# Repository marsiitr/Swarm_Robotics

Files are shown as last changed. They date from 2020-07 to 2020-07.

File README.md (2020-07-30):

# Swarm_Robotics
## Srishti 2020
<p align="center">
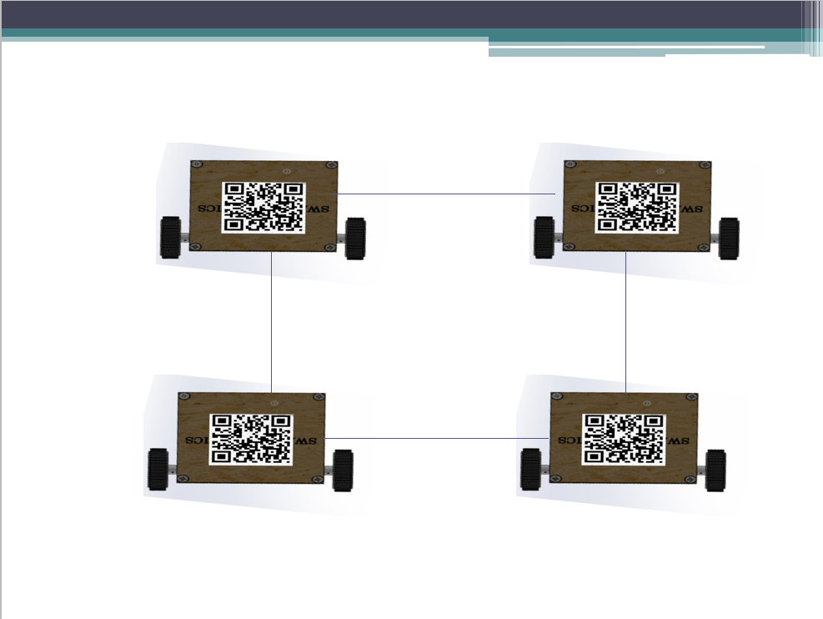
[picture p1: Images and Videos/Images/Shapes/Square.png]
  
</p>

## Abstract
<p align ="justify">Swarm robotics is an approach to the coordination of the multiple robots as a system which consist of large numbers of mostly simple physical robots.  Only through their interactions a collective behavior emerges that is able to solve complex tasks. These characteristics lead to the main advantages of swarms: adaptability, robustness, and scalability. Under this excuse we made multiple bots which coordinate among themselves to form different shapes.</p>

## Motivation
<p align ="justify">As swarm of ants work in unison to achieve an intimidating task, similarly multiple bots can work in unison to achieve a seemingly difficult task. As the newbies, out of curiosity we choose to work on the same.</p>

## Working
<p align ="justify">Open cv facilitates the process of reading QR codes, including loading images from disk, grabbing a new frame from a video stream, and processing it. Important libraries we imported are pyzbar, argparse and cv2.
    The ZBar library will decode the barcode or QR code. OpenCV can come back in to perform any further processing and display the result. For Python, we use pyzbar, which has a simple decode function to locate and decode all symbols in the image. The decode function simply wraps pyzbar’s decode function and loops over the located barcodes and QR codes and prints the data. The decoded symbols from the previous step are passed on to the display function . If the points form a quad ( e.g. in a QR code ), we simply draw the quad. If the location is not a quad, we draw the outer boundary of all the points ( also called the convex hull ) of all the points. This is done using an OpenCV function called cv2.convexHull. Finally, the main function simply reads an image, decodes it and displays the results.</p>
<p align="center">
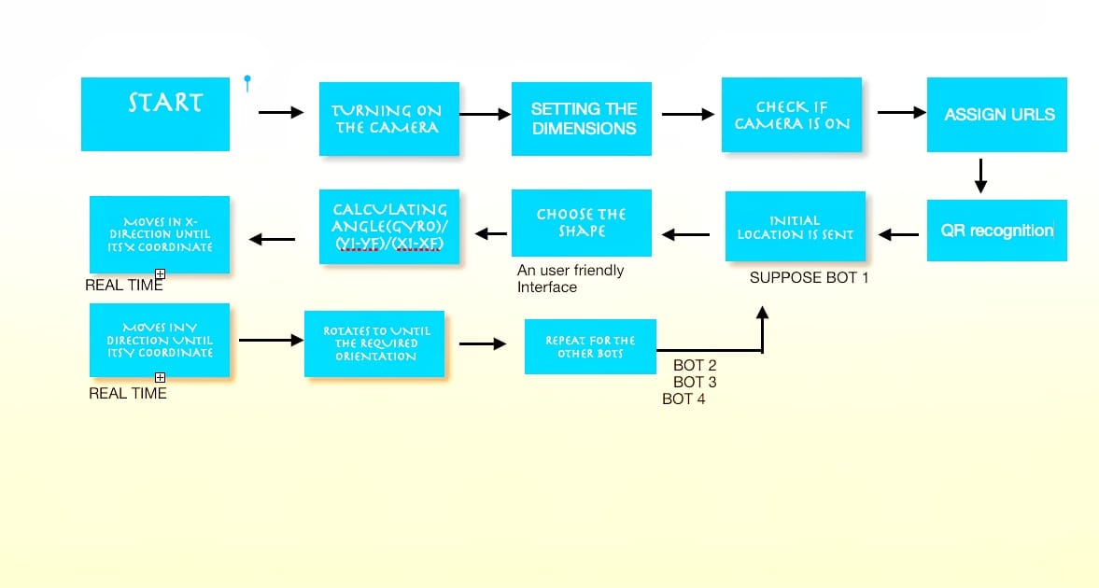
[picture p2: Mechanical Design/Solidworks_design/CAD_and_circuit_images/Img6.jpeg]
  
</p>
<p align ="justify">Firstly ,a function handleSpecificArg() is defined that receives data that is sent by the python code that is doing image recognition. Python returns the data in the form of string which is then sent to the NodeMCU. All of the NodeMCUs are connected to the hotspot of the same laptop so it directly sends the data to each NodeMCU.
  Then several functions such that backward(), forward(), etc are defined that helps the bots to move. Then a function get_gyro() is defined that gives the angle turned by bot. Then setup of different pins takes place. Then the function data() gets all the coordinates and the current angle from x-axis and which shape is to be made.
Then the real loop function starts. First we get data from the camera . Then the bot starts to rotate until it is turned in the direction of target position . Then it starts to move forward until it reaches the target position on reaching the target position it starts rotating until it reaches the required orientation. All the bots do the same to make the required shape.</p>

## Mechanical Aspect of the Design
<p align ="justify">This project consists of four mechanically identical bots which move in unison to form the shape specified by the user. But each of the bot has a unique identity because of the unique QR code pasted on its roof.</p>
<p align="center">
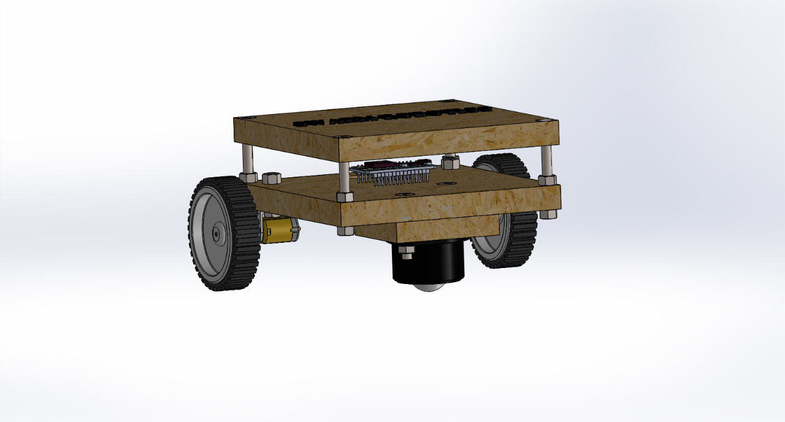
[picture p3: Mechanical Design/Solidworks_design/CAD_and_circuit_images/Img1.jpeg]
  
</p>

<p align ="justify">Each bot has 2 sheets of ply one over the other with electrical components between them. A single bot consists of 2 normal wheels at the back, 1 castor wheel at the front and 2 L-brackets for holding motors in them.</p>

<p align="center">
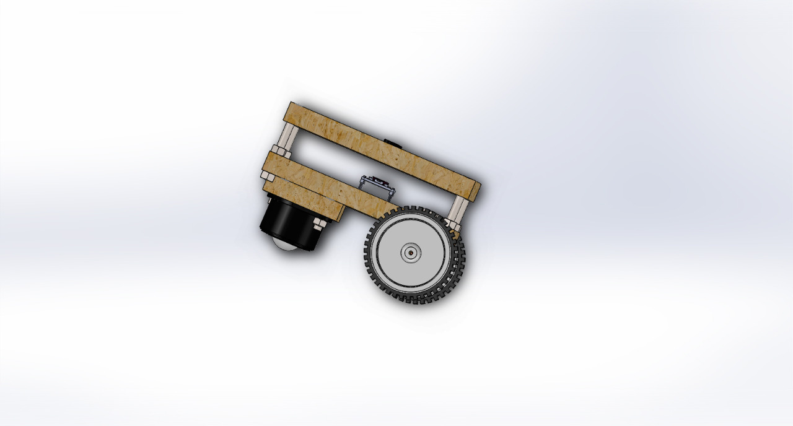
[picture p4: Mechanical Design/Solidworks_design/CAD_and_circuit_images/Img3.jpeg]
  
</p>

## Electronics Aspect of the Design
<p align ="justify">In each of the bot, the microcontroller used is ESP8266(NodeMCU). For angle detection fron the initial position for a particular bot, a gyroscope sensor(particularly MPU-92/65 is used. For controlling the motors, a motor driver(particularly L298) is used in each bot.</p>
<p align="center">
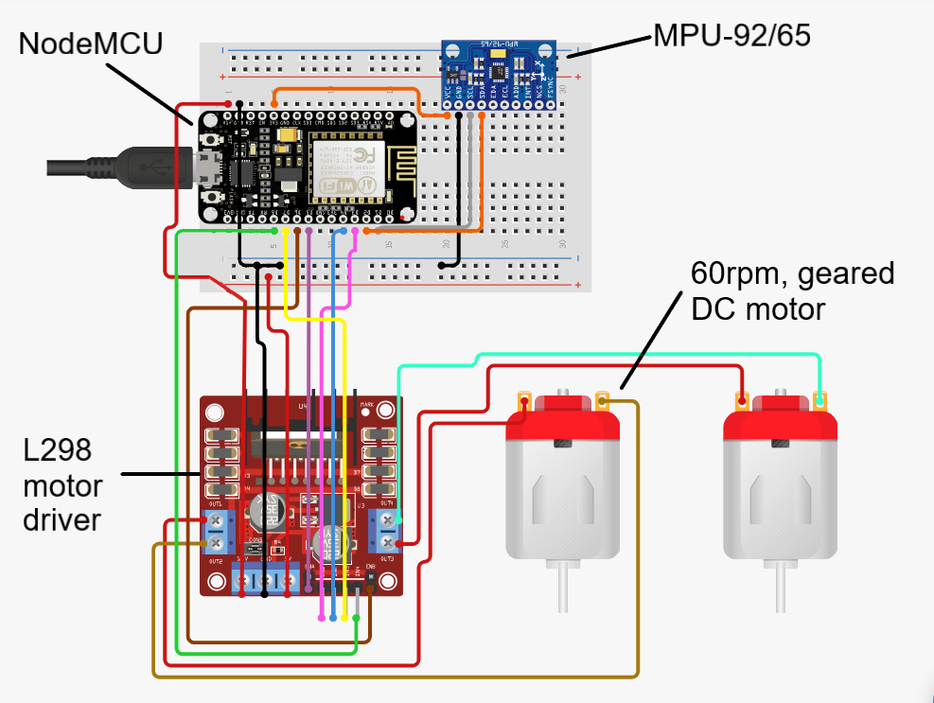
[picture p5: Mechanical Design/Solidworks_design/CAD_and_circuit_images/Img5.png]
  
</p>
  <p align ="justify">Initially each bot is set to a particular same direction, but when the user calls for a shape using a user friendy interface, each bot is assigned its final coordinates in the field of view of the overhead camera. Thus each bot reaches to its final position one by one. And the final shape is achieved.</p>

## Cost Structure

| Part | Quantity | Cost per unit | Total cost |
|---|:---:|:---:|---:|
| ESP8266 (NodeMCU) | 4 | 330 | 1320 |
| L298  (Motor Driver) | 4 | 250 | 1000 |
| 60rpm DC Motor | 8 | 200 | 1600 |
| MPU 92/65 (Gyroscope) | 4 | 300 | 1200 |
| Overhead Camera (WebCam) | 1 | 3000 | 3000 |
| 12V Li-polymer Battery | 4 | 2000 | 8000 |
| Jumpers | 60 | 5 | 300 |
| Nut & Bolt (Medium) | 16 | 5 | 80 |
| Nut & Bolt (Long) | 16 | 10 | 160 |
| L - Brackets | 8 | 15 | 120 |
| Normal Wheels | 8 | 30 | 240 |
| Castor Wheels | 4 | 25 | 100 |
| PlyWood | 1 | 280 | 280 |
| Miscellaneous | - | - | 600 |
| Total | | | Rs.18000/- |

## Applications
Potential applications of swarms are many. To list the few:
* Tasks that demand miniaturization, like distributed sensing tasks in micromachinery or the human body.
* One of the promising use of the swarms is in disaster rescue missions.
* Swarms can be used in traffic handling.
* Swarms can form different shapes and designs so they can reach forbidden area.

## Limitations
* Formation of limited number of shapes.
* Initial relative distance  of the bots depends on the field of view of the camera use.
* Dependency on QR code recognition.
* Gyroscope must be used with intense care, as a slight slip of gyro in any of the direction, may give a large error in angle calculation.

## Future Improvement
* Many more shapes can be added to the list.
* Providing the sensors to prevent collision.
* Use of PID, to improve the movement of the bots.
* Assembling(to form the shape), independent of their initial positions.
* Use of GPS instead, to reach their destination.

## Team Members

1. [Paritosh Sanadhya](https://github.com/Pasa1912)
2. [Prathamesh Bhaktan](https://github.com/prathamb)
3. [Samiksha Jain](https://github.com/samiksha-jain003)
4. [Sarthak Malik](https://github.com/ganzagun)
5. [Vidhi Mittal](https://github.com/Vidhi-mittal01)

## Mentors
1. [Annu Shree](https://github.com/annushree21)
2. [Shubhanshu Agarwal](https://github.com/Shubhanshu07)

## References
* [OpenCV Python Tutorial For Beginners](https://www.youtube.com/playlist?list=PLS1QulWo1RIa7D1O6skqDQ-JZ1GGHKK-K)
* [Stack Overflow](https://stackoverflow.com/)
* [Pyimagesearch](https://pyimagesearch.com/)
* [Arduino](https://www.arduino.cc/)

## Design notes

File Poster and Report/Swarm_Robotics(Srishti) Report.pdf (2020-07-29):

# REPORT

# Event: Srishti 2020 Indian Institute Of Technology Roorkee

# Project name: Swarm Robotics

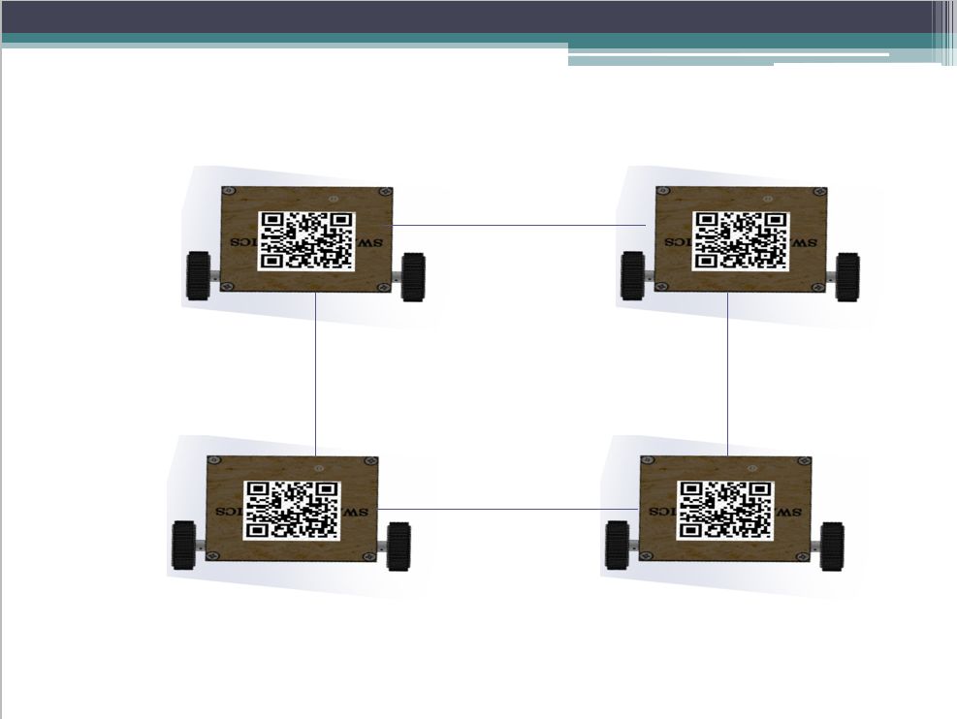
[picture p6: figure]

# Team Members and Mentors :

Team Members | Enroll. no.
Paritosh Sandhaya | 19115083
Prathmesh Bhaktan | 19117088
Samiksha Jain | 19312028
Sarthak Malik | 19118073
Vidhi Mittal | 19113156

# Mentors

## Shubhanshu Agarwal Annu Shree

# OVERVIEW

Every year Models And Robotics Section (MARS) IIT ROORKEE organises annual technical fest “SRISHTI”, especially for freshers, where they can sharpen their technical and entrepreneurial skills.
Group of few diligent members are assigned to certain projects within a few months, under the mentorship of intuitive MARS members. We got the window of opportunity to be the part of this technical fest where we came out of the idea of building swarm robots , which coordinate among themselves to form various shapes which includes square, triangle, some alphabets and numbers etc.

# MOTIVATION

As a swarm of ants work in unison to achieve an intimidating task, similarly a swarm of robots can work in unison to achieve seemingly impossible tasks. As the enthusiastic newbies we were fascinated by this idea and decided to work on the same.

# ABSTRACT

Swarm robotics is an approach to the coordination of the multiple robots as a system which consists of large numbers of mostly simple physical robots. Only through their interactions a collective behavior emerges that is able to solve complex tasks. These characteristics lead to the main advantages of swarms: adaptability, robustness, and scalability. Under this excuse we made multiple bots which coordinate among themselves to form different shapes.

# WORKING

↓

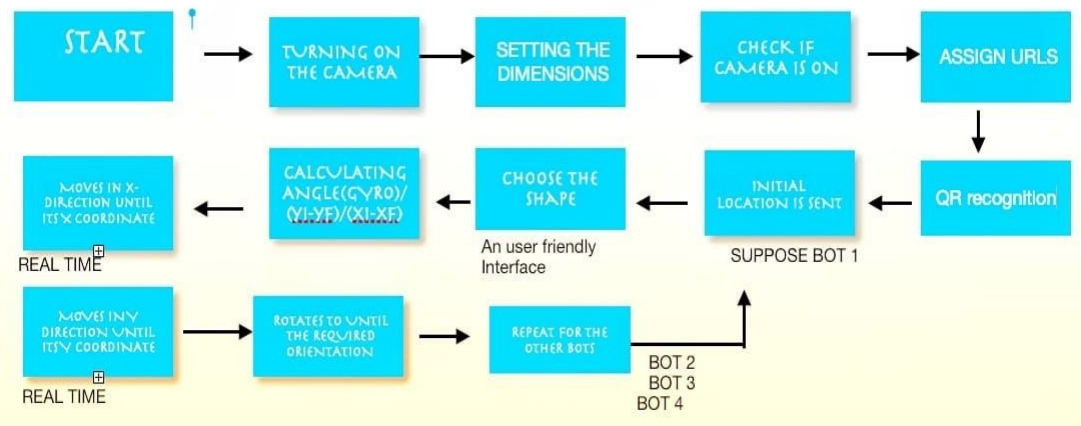
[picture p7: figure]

# Mechanical Aspect of the design:

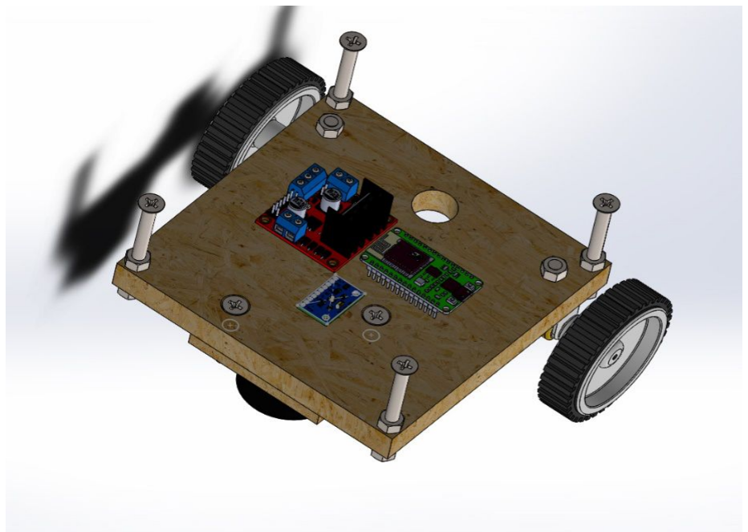
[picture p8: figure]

Angled view of the bot

## Details of Components Used:

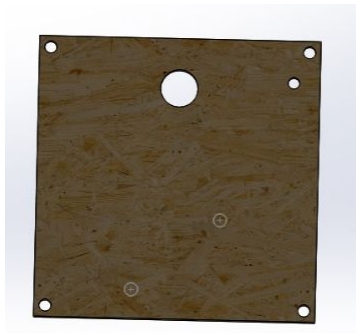
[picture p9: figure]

## 1. Plywood

Larger Plywood acts as a base for assembling all parts of swarm robots and provides support to all items. It has a size of 150x150x15 mm, and has a hole of 20mm on it for connecting motors with Arduino.

Larger Plywood is also used to make roof of robot which has QR Codes for scanning purpose

Smaller plywood is used to level the castor wheel with normal wheels and provide stability to bot.

Its size depends on the size of castor wheel , in our case, from the standard cad model of caster wheel, the thickness of smaller plywood is 13.8mm.

## 2.L-brackets

L-brackets are used for mounting motors and holding it in the correct fixed position. It is mounted on a plywood base with the help of 3mm nuts and bolts.

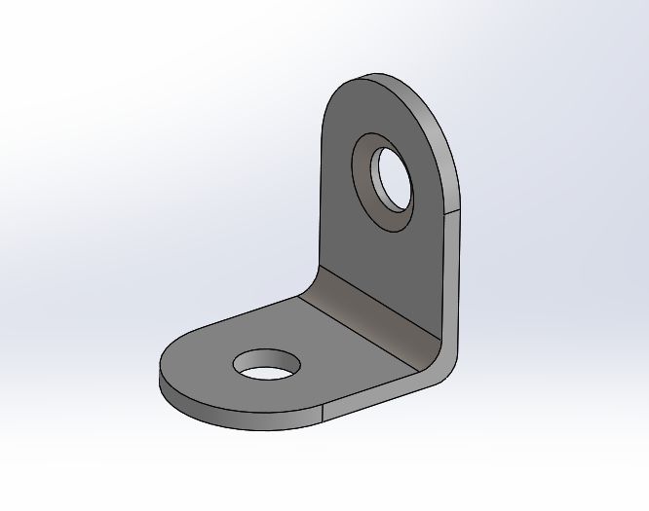
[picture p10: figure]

## 3. Castor Wheel

Castor wheel is used in the front part of the robot to provide all direction movement to the robot.

It is mounted below base
plywood with help of another ply

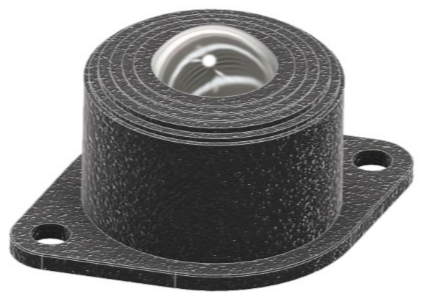
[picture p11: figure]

of appropriate thickness to level castor wheel with normal wheels. Nut and bolt are used for mounting.

## 4.70mm Wheels

Wheels are used to provide mobility to the robot. It is directly attached to the motor and a screw is tightened to the motor shaft to prevent the wheels from coming out while the robot is moving.

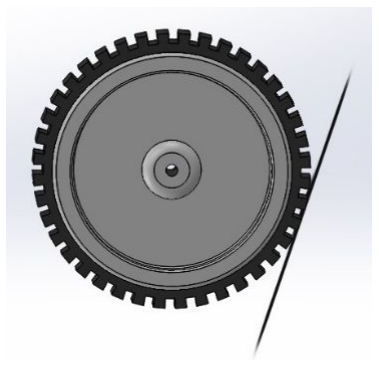
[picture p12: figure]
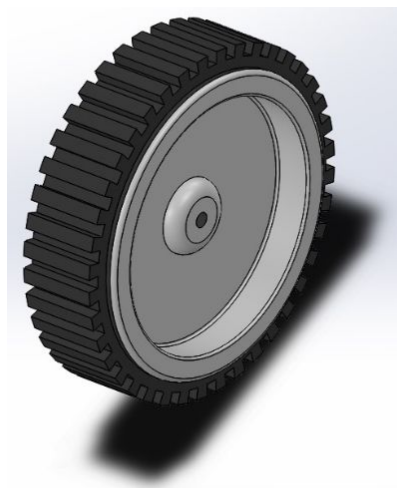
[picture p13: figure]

Wheel size used in our robot is of 70mm diameter and 20mm thickness which is the size of standard robot wheels available in the market.

## 5.Nut And Bolts

Nut and bolts are used to fix L-brackets, Castor wheels in the position .

It is also used to keep the roof of the robot at a certain height above base so that it doesn’t interface with any electronic parts. For fixing

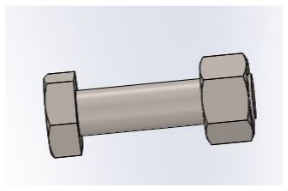
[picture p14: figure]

Caster wheel and L-brackets nut and countersink of size 3mm is used.

For keeping the roof at a certain height, a nut and countersink of size 6 mm diameter is used, with one nut below base and one on base as shown in figure.

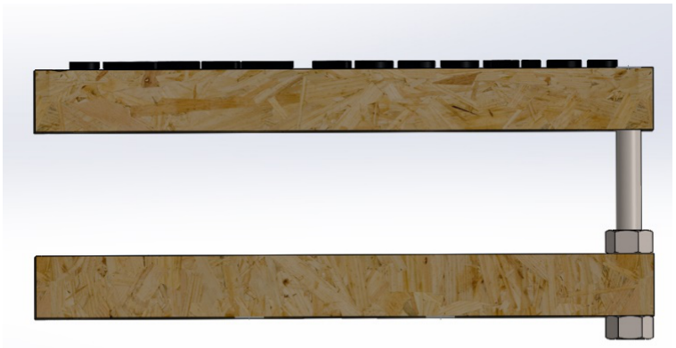
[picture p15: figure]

Figure

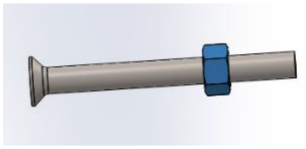
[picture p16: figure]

Here the countersink
is used as the head of the countersink gets embedded
in plywood and thus there is no protruding head in the
roof of the robot.

# Electronics Aspect of the Design:

## Details of Components Used:

## 1. Microcontroller:

A microcontroller is a compact integrated circuit designed to govern a specific operation in an embedded system. In this project, we need a microcontroller that can receive information in wireless mode. So, we used a
NodeMCU in this project.

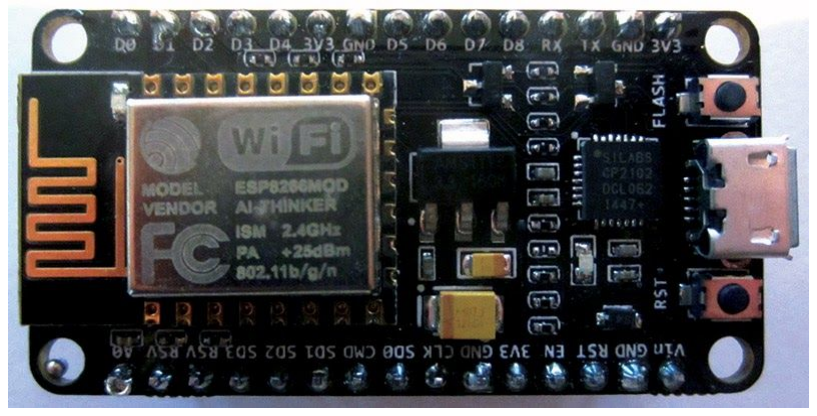
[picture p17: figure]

NodeMCU is an open
source firmware for which
open source prototyping
board designs are available. The name "NodeMCU"
combines "node" and "MCU"
(micro-controller unit).

The model we used is ESP8266 NodeMCU.The ESP8266 WiFi Module is a self contained SOC with integrated TCP/IP protocol stack that can give any microcontroller access to your WiFi network. The ESP8266 is capable of either hosting an application or offloading all Wi-Fi networking functions from another application processor.

In our project, we not only used it for data transfer from the host to an individual bot but also as a substitute for an ordinary Arduino microcontroller unit.

## 2.Gyroscopic Sensor

Gyroscope sensor is a device that can measure and maintain the orientation and angular velocity of an object. These are more advanced than accelerometers. These can measure the tilt and lateral orientation of the object whereas an accelerometer can only

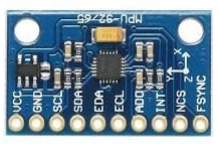
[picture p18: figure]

measure linear motion.

The concept of Coriolis force is used in Gyroscope sensors. In this sensor to measure the angular rate, the rotation rate of the sensor is converted into an electrical signal.
In this project, we used the MPU-92/65 model of gyroscope sensor. The gyroscope sensor gives us the angle rotated by the bot i.e. Angle between the direction of bot at time t and the initial direction of the bot.

## 3. Motor - Driver :

A motor driver is an integrated circuit that makes the motor move as per the given instructions or the inputs (high and low). It listens to the low voltage from the controller/processor and controls an actual motor which needs high input voltage.

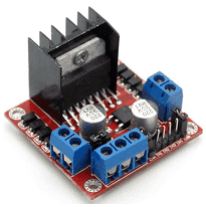
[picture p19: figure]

The model of the motor-driver we
used is L298. This motor-driver can control
2 DC motors at the same time. So we need a single motor driver for each bot. While connecting a motor driver to a battery, it must be carefully noted that the positive terminal of the motor driver must be connected to the positive terminal of the battery, and vice versa. Otherwise, it might cause damage to the motor-driver.

## 4.DC-motors :

The electric motor operated by direct current(DC) is called DC motor. This is a device that converts DC electrical energy into a mechanical energy. This type of motor comes in different rantings of Torques and
RPM(maximum Rotation per minute)

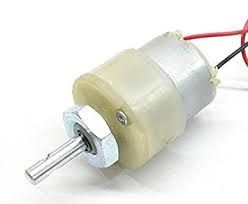
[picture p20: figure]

In this project, we used a 60 rpm DC metal geared motor. For each of the bot, we need 2 DC motors.

# Electrical Connections :

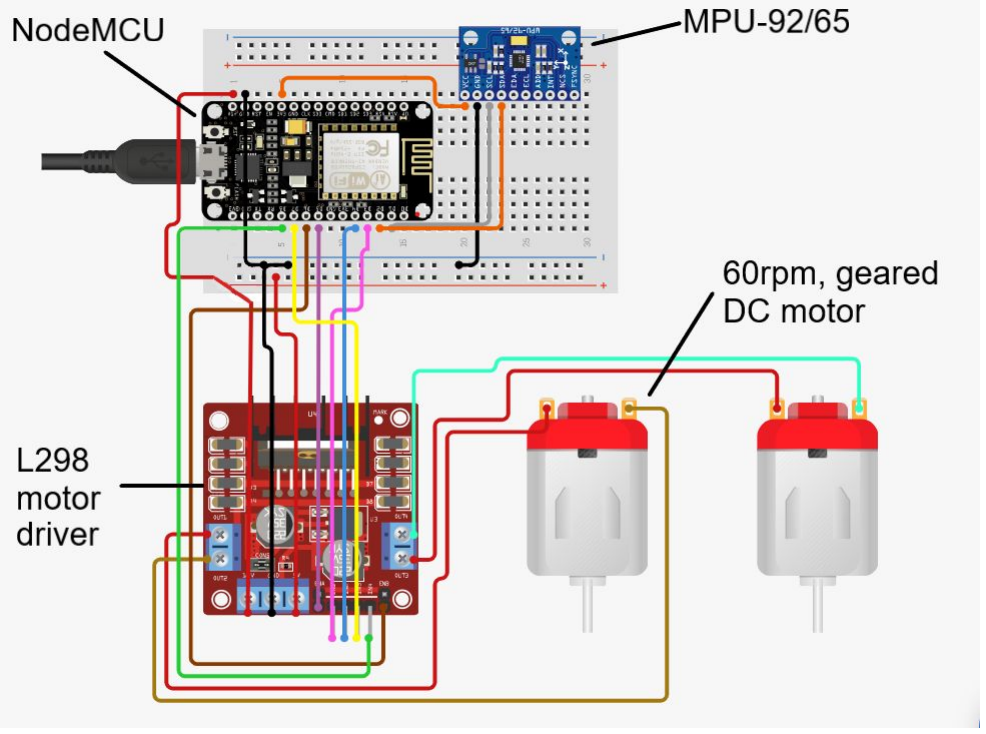
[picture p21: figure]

The electrical connections should as shown in the figure. But it should be noted that the figure is for connectivity purposes only. In actuality, gyroscope when connected to the microcontroller via jumpers, shows non negligible error in angle detection. So, while using the gyro with the microcontroller, we need to solder a perfboard to connect the gyro with the microcontroller. Thus in actuality, we use a soldered perfboard at the place of breadboard.

# STEPS:-

## 1. Placing components

A. Place NodeMCU
B. Place DCMDriverL298
C. Place DCMotor_A
D. Place DCMotor_B
E. Place MPU9265

## 2. Connect NodeMCU

- NodeMCU1 GND to Bus GND

## 3. Connect DCMDriverL298

- DCMDriverL298 OUT1 to DCMotor_A Coil2
- DCMDriverL298 OUT2 to DCMotor_A Coil1
- DCMDriverL298 OUT3 to DCMotor_B Coil2
- DCMDriverL298 OUT4 to DCMotor_B Coil1
- DCMDriverL298 12V to Bus POS
- DCMDriverL298 5V to NodeMCU Vin (Power Input of NodeMCU)
- DCMDriverL298 ENA to NodeMCU1 D5

- DCMDriverL298 ENB to NodeMCU1 D6
- DCMDriverL298 GND to Bus GND
- DCMDriverL298 INT1 to NodeMCU1 D3
- DCMDriverL298 INT2 to NodeMCU1 D4
- DCMDriverL298 INT3 to NodeMCU1 D7
- DCMDriverL298 INT4 to NodeMCU1 D8

## 4. Connect MPU9255

- MPU9255 GND to Bus GND
- MPU9255 SCL to NodeMCU1 D1(On perfboard using male and female headers)
- MPU9255 SDA to NodeMCU1 D2(On perfboard using male and female headers)
- MPU9255 VCC to NodeMCU1 3V3

## 5. Connect Battery and Switch

- Connect BUS POS to the positive terminal of the battery.
- Connect BUS GND to the switch and then the negative terminal of the battery.

# Real-time QR code reading with OpenCV

Open cv facilitates the process of reading QR codes, including loading images from disk, grabbing a new frame from a video stream, and processing it. Important libraries we imported are pyzbar, argparse and cv2. The ZBar library will decode the barcode or QR code. OpenCV can come back in to perform any further processing and display the result. For Python, we use pyzbar, which has a simple decode function to locate and decode all symbols in the image. The decode function simply wraps pyzbar’s decode function and loops over the located barcodes and QR codes and prints the data. The decoded symbols from the previous step are passed on to the display function . If the points form a quad ( e.g. in a QR code ), we simply draw the quad. If the location is not a quad, we draw the outer boundary of all the points ( also called the convex hull ) of all the points. This is done using an OpenCV function called cv2.convexHull. Finally, the main function simply reads an image, decodes it and displays the results.

# Role of ESP8266

Firstly ,a function handleSpecificArg() is defined that receives data that is sent by the python code that is doing image recognition. Python returns the data in the form of string which is then sent to the NodeMCU. All of the NodeMCUs are connected to the hotspot of the same laptop so it directly sends the data to each NodeMCU.

Then several functions such that backward(), forward(), etc are defined that helps the bots to move. Then a function get_gyro() is defined that gives the angle turned by bot. Then setup of different pins takes place. Then the function data() gets all the coordinates and the current angle from x-axis and which shape is to be made.

Then the real loop function starts. First we get data from the camera . Then the bot starts to rotate until it is turned in the direction of target position . Then it starts to move forward until it reaches the target position on reaching the target position it starts rotating until it reaches the required orientation. All the bots do the same to make the required shape .

# Cost Structure

Part | Quantity | Cost per unit | Total cost
ESP9266 (NodeMCU) | 4 | 330 | 1320
L298 (Motor Driver) | 4 | 250 | 1000
60rpm DC Motor | 8 | 200 | 1600
MPU 92/65 (Gyroscope) | 4 | 300 | 1200
Overhead Camera (WebCam) | 1 | 3000 | 3000
12V Li-polymer Battery | 4 | 2000 | 8000
Jumpers | 60 | 5 | 300
Nut & Bolt (Medium) | 16 | 5 | 80
Nut & Bolt (Long) | 16 | 10 | 160
L - Brackets | 8 | 15 | 120
Normal Wheels | 8 | 30 | 240

Castor Wheels | 4 | 25 | 100
PlyWood | 1 | 280 | 280
Miscellaneous | - | - | 600
Total | | | Rs.18000/-

# APPLICATIONS

❏ Tasks that demand miniaturization, like distributed sensing tasks in micro machinery or the human body.

❏ Swarms can be used in traffic handling.

❏ Swarms can form different shapes and designs so they can reach forbidden areas.

❏ One of the promising uses of the swarms is in disaster rescue missions.

❏ SWARMS CAN BE USED AMID PANDEMIC BREAK DOWN(COVID 2019): As these swarms can provide all the necessary stuff to the patients,which can prevent doctors and medical staff from coming in direct contact with them.

# Limitations

- Formation of a limited number of shapes.
- Initial relative distance of the bots depends on the field of view of

the camera use.

- Dependency on QR code recognition.
- Gyroscope must be used with intense care, as a slight slip of gyro

in any of the directions, may give a large error in angle calculation.

# References

- OpenCV Python Tutorial For Beginners -

https://www.youtube.com/playlist?list=PLS1QulWo1RIa7D1O6skq

DQ-JZ1GGHKK-K (https://www.youtube.com/playlist?list=PLS1QulWo1RIa7D1O6skqDQ-JZ1GGHKK-K)

- Stack Overflow - https://stackoverflow.com/
- Pyimagesearch - https://pyimagesearch.com/
- Arduino - https://www.arduino.cc/

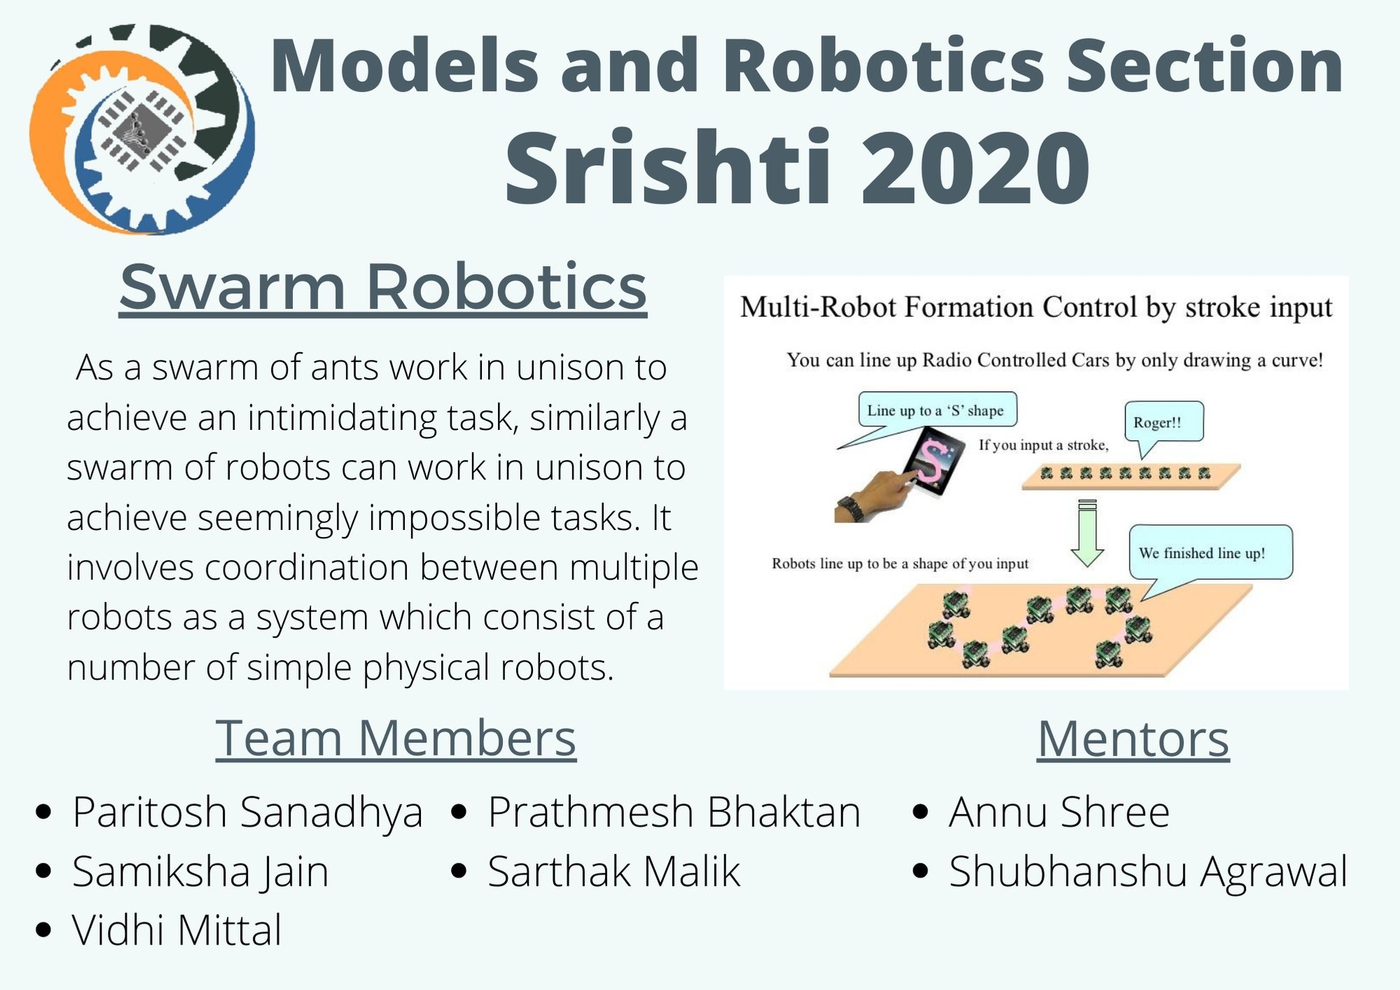
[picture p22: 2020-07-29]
Poster and Report/Swarm_Poster.jpg

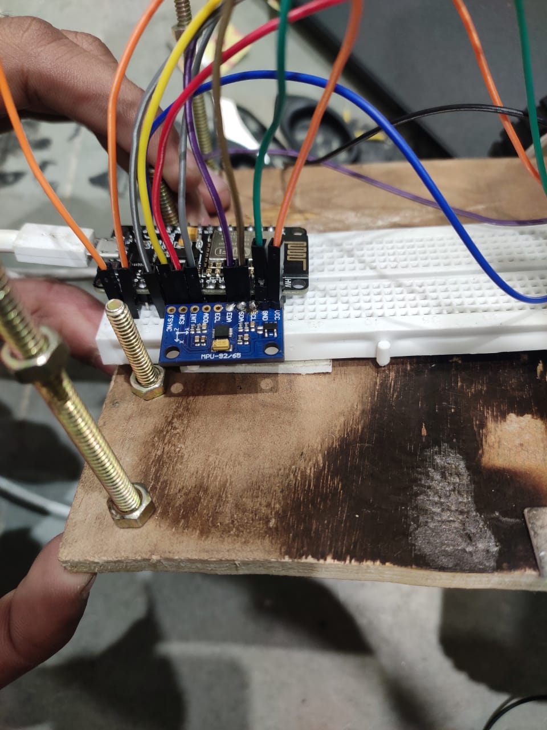
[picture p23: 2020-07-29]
Images and Videos/Images/Bot_images/Real_Bot_3.jpeg

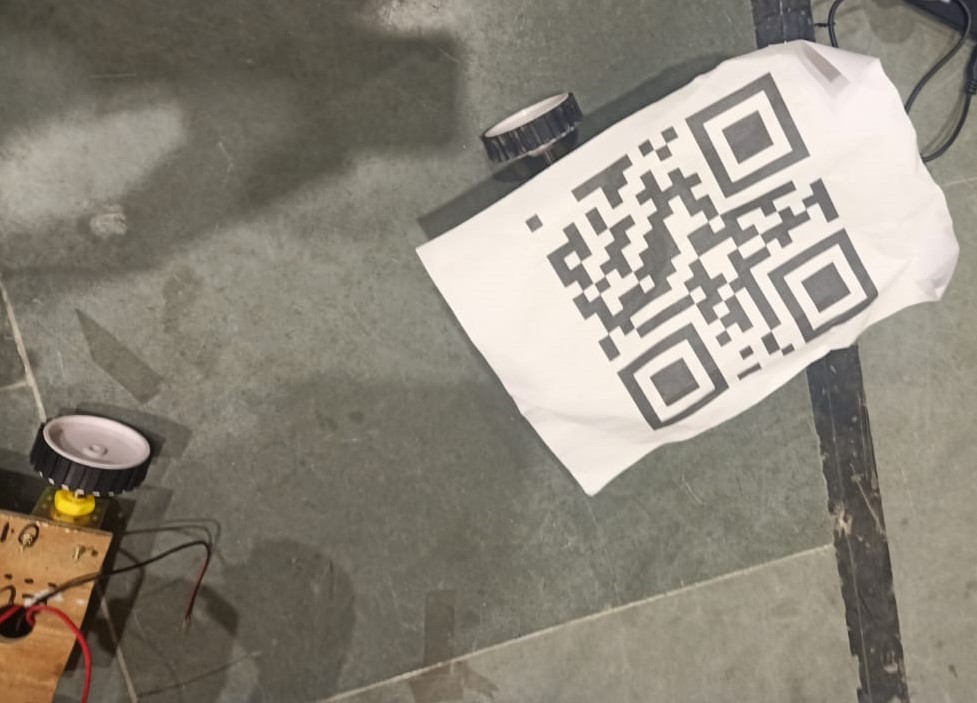
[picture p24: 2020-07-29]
Images and Videos/Images/Bot_images/Real_Bot_4.jpeg

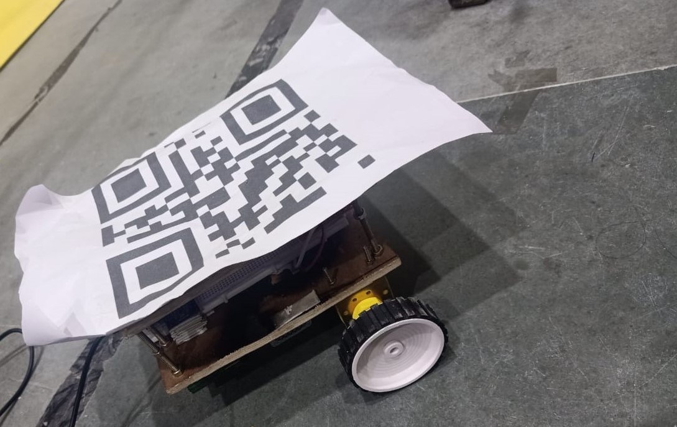
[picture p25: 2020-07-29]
Images and Videos/Images/Bot_images/Real_Bot_2.jpeg

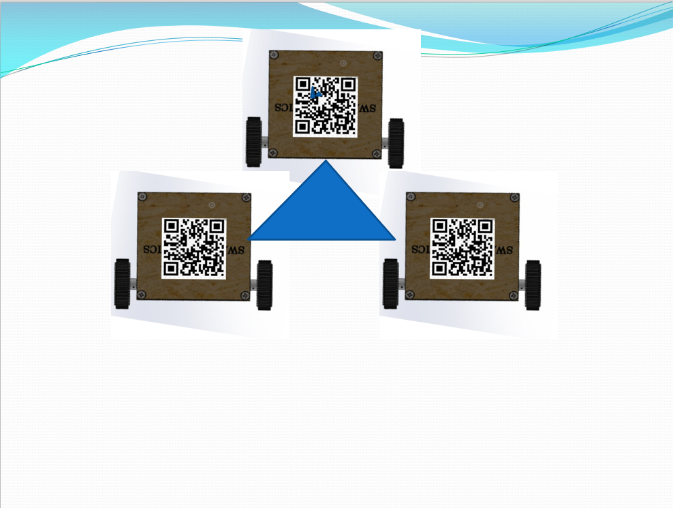
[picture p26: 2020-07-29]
Images and Videos/Images/Shapes/Triangle.png

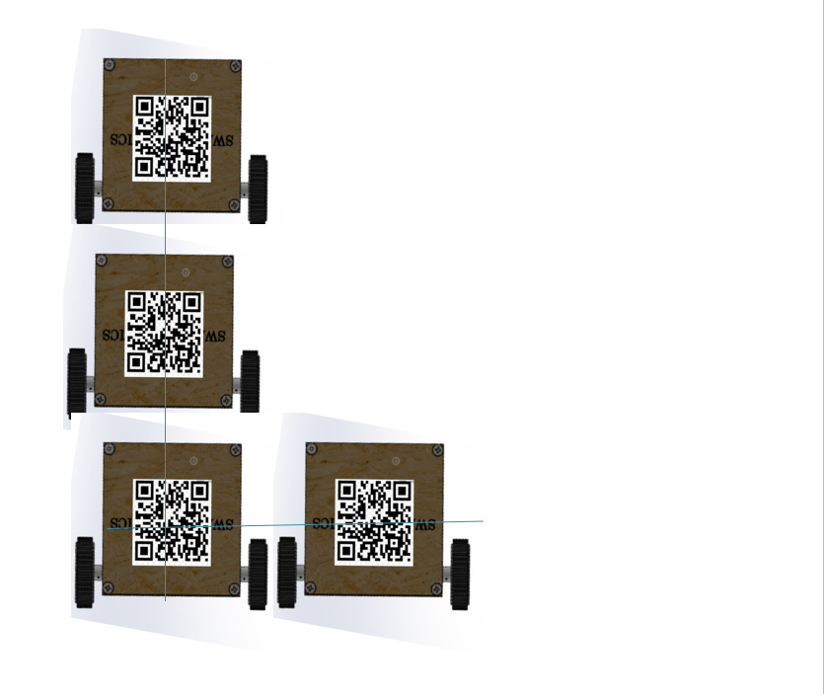
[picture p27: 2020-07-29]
Images and Videos/Images/Shapes/L-shape.png

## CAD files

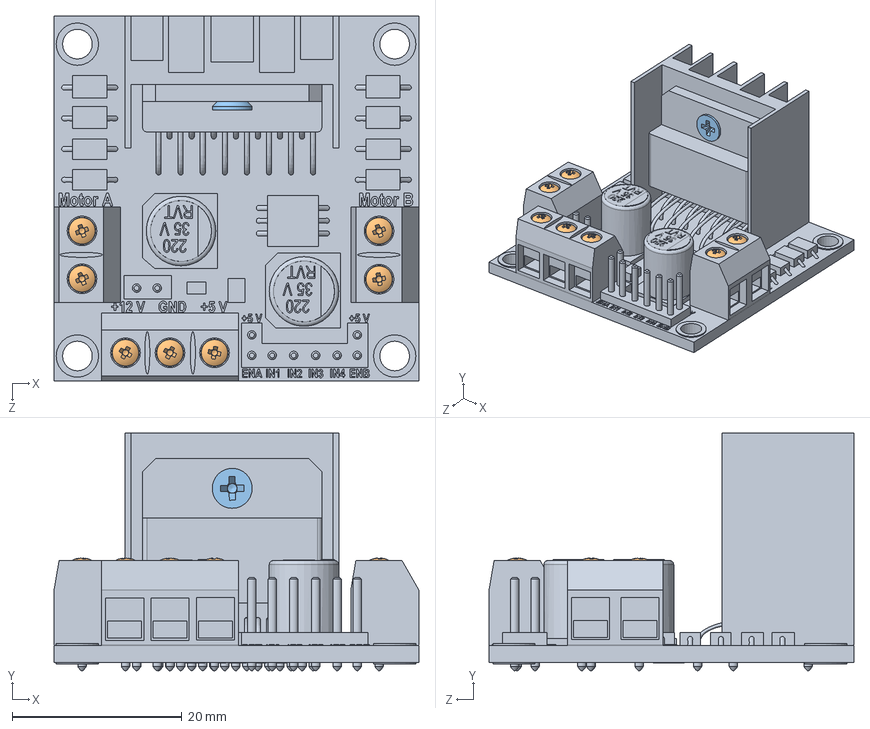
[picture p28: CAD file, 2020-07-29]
Mechanical Design/Solidworks_design/l298n-stepper-motor-driver-red-1.snapshot.3/L298N Stepper Motor Driver (Red).SLDASM
43.0 x 28.0 x 43.0 mm
L298N Stepper Motor Driver (Red)
pan head cross recess screw_iso x 7
countersunk flat head cross recess screw_iso

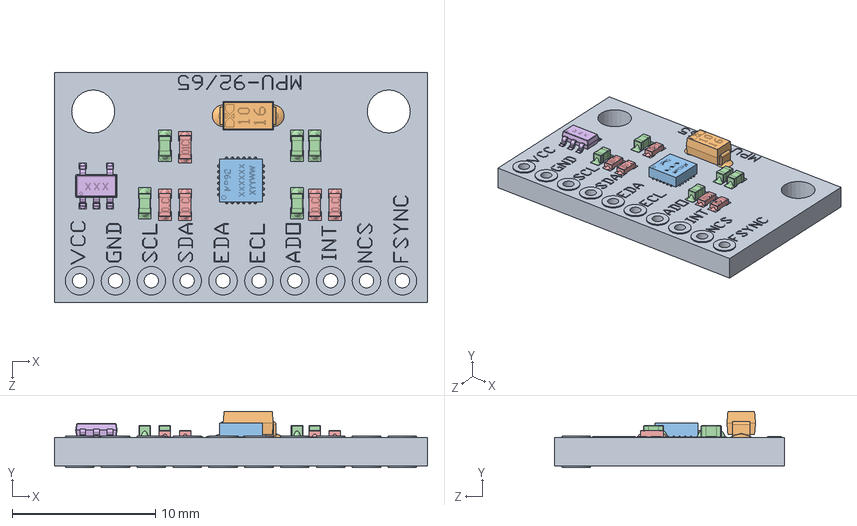
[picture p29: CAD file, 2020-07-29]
Mechanical Design/Solidworks_design/mpu-92-65-1.snapshot.2/MPU 92_65/MPU9250.SLDASM
26.0 x 3.91 x 16.0 mm
PCB
C2
MP92
C1 x 5
R1 x 5
V1

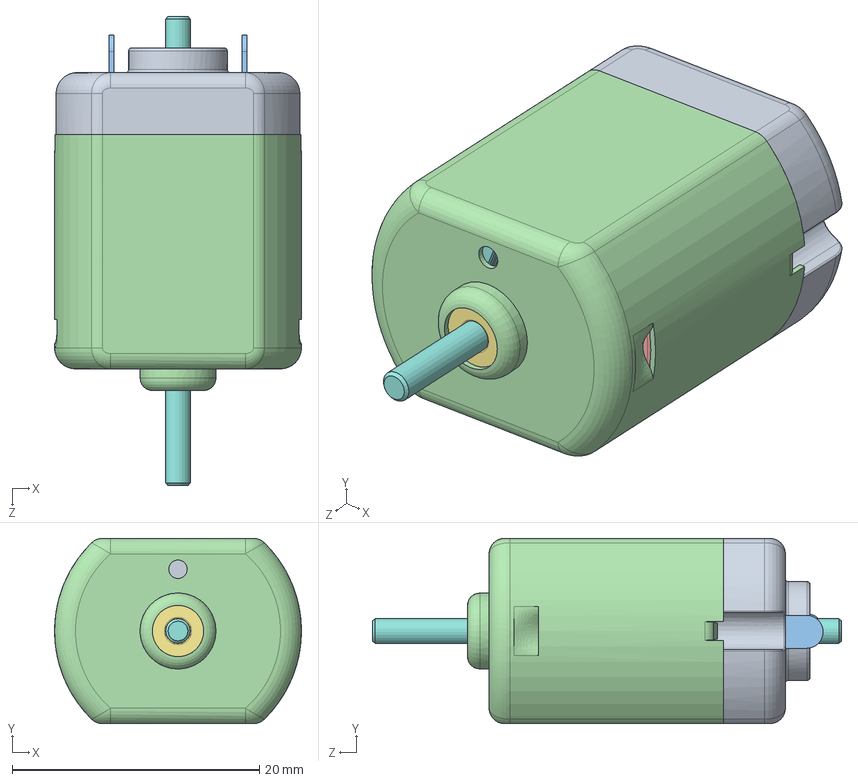
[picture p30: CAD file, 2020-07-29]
Mechanical Design/Solidworks_design/dc-motor-2/motor/motor assembly.SLDASM
20.0 x 15.0 x 38.0 mm
arbor 1

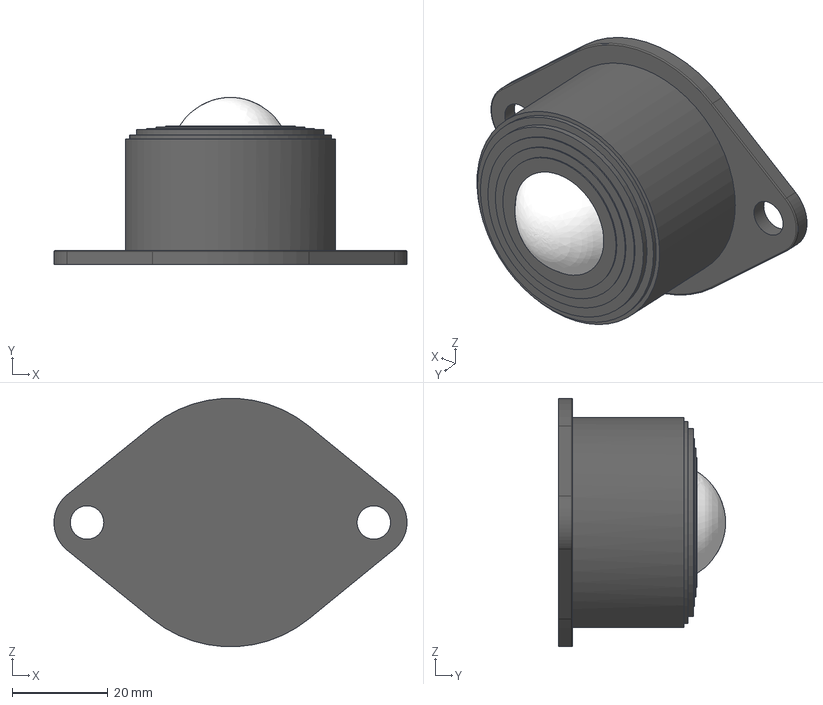
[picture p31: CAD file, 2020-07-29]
Mechanical Design/Solidworks_design/caster-metal-wheel-1.snapshot.2/Caster Wheel.stp
73.8 x 35.0 x 51.9 mm

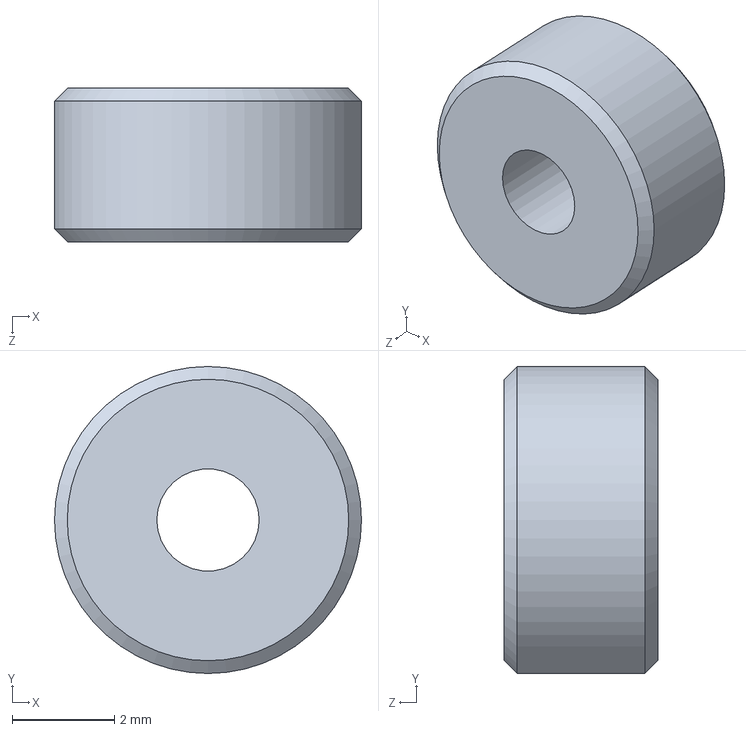
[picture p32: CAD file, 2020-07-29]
Mechanical Design/Solidworks_design/dc-motor-2/motor/Part6.SLDPRT
6.00 x 6.00 x 3.00 mm

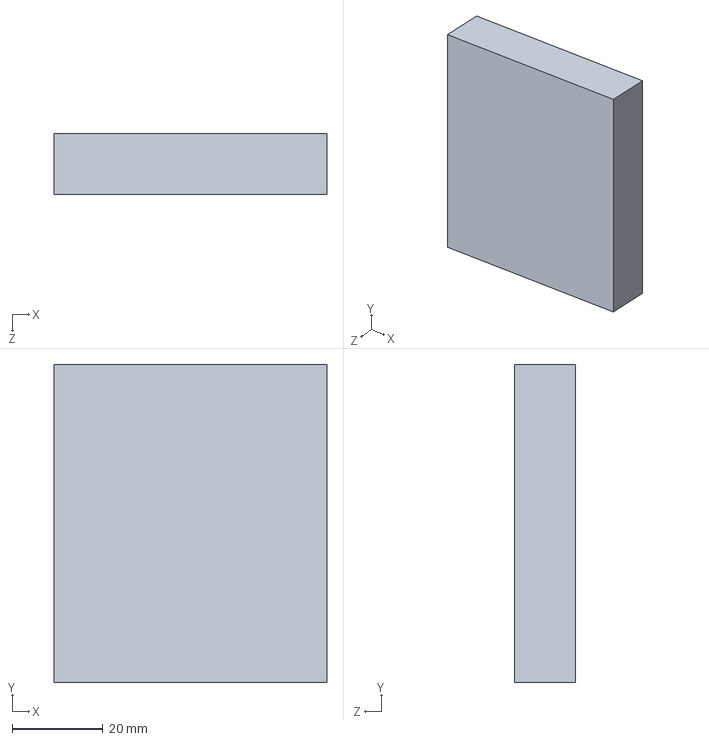
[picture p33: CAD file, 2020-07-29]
Mechanical Design/Solidworks_design/height stable.SLDPRT
60.0 x 70.0 x 13.5 mm

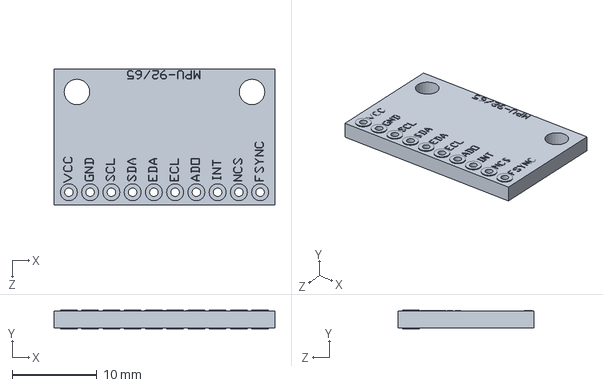
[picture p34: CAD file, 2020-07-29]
Mechanical Design/Solidworks_design/mpu-92-65-1.snapshot.2/MPU 92_65/PCB.SLDPRT
26.0 x 2.20 x 16.0 mm

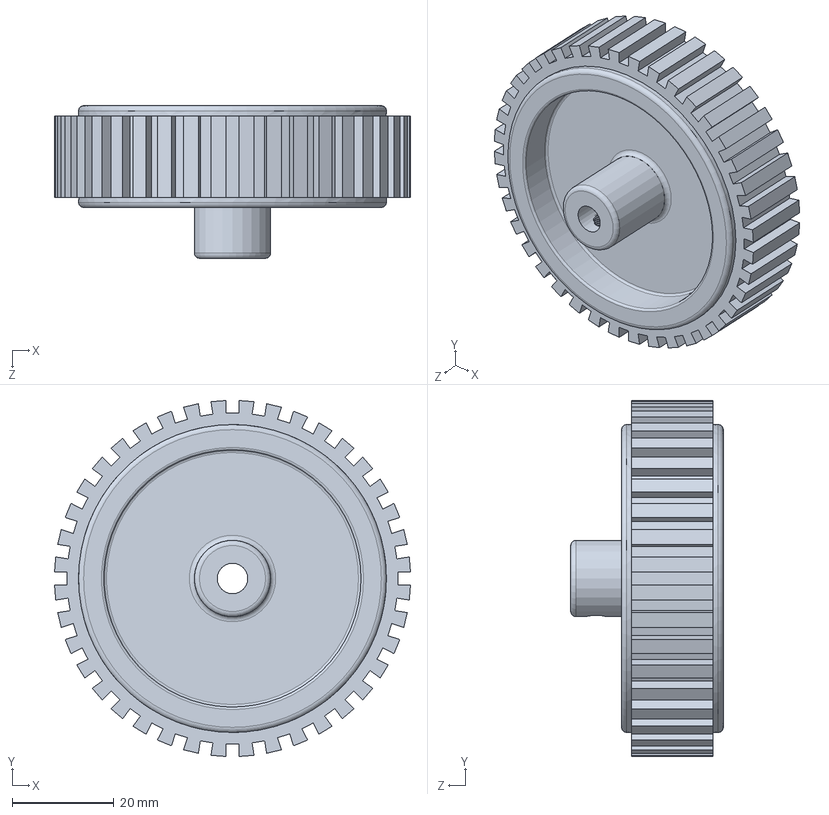
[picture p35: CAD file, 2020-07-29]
Mechanical Design/Solidworks_design/robo-s-wheel-1.snapshot.2/tyre.SLDPRT
70.0 x 70.0 x 30.0 mm

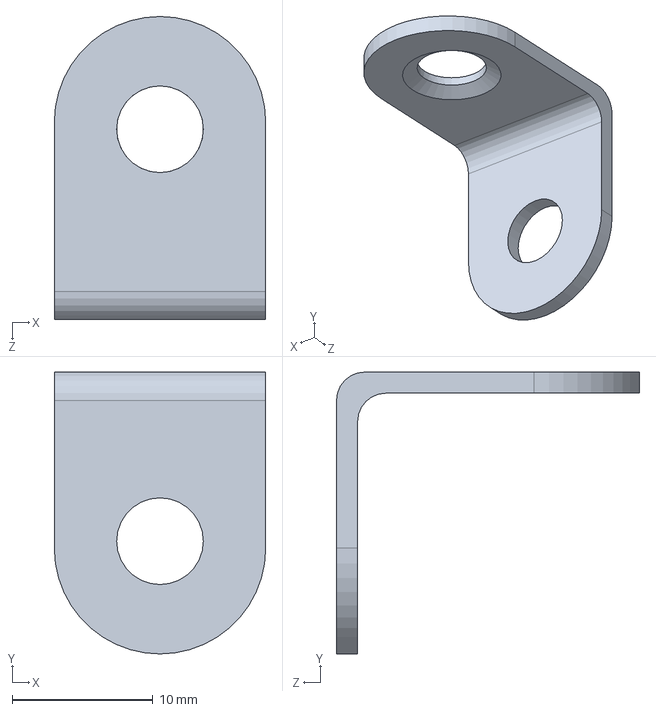
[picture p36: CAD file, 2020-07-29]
Mechanical Design/Solidworks_design/steel-angle-bracket-1.snapshot.2/angled part.SLDPRT
15.0 x 20.0 x 21.5 mm

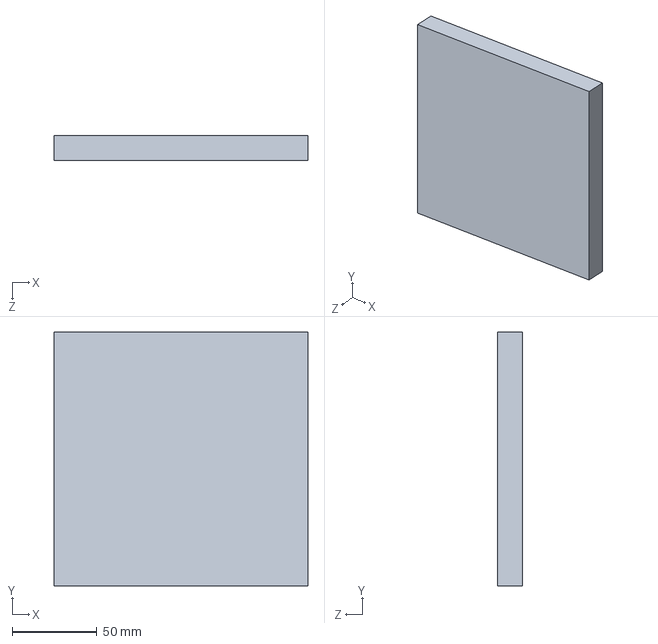
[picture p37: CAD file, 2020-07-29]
Mechanical Design/Solidworks_design/base.SLDPRT
150.0 x 150.0 x 15.0 mm

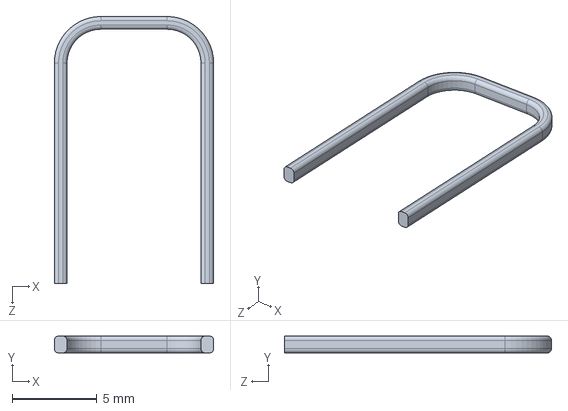
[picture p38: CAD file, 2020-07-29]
Mechanical Design/Solidworks_design/dc-motor-2/motor/Part5.SLDPRT
9.40 x 1.00 x 15.8 mm

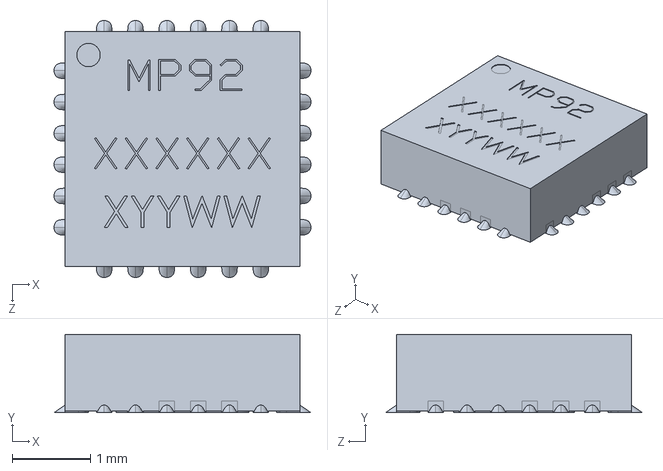
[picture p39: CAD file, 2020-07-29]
Mechanical Design/Solidworks_design/mpu-92-65-1.snapshot.2/MPU 92_65/MP92.SLDPRT
3.28 x 1.00 x 3.28 mm

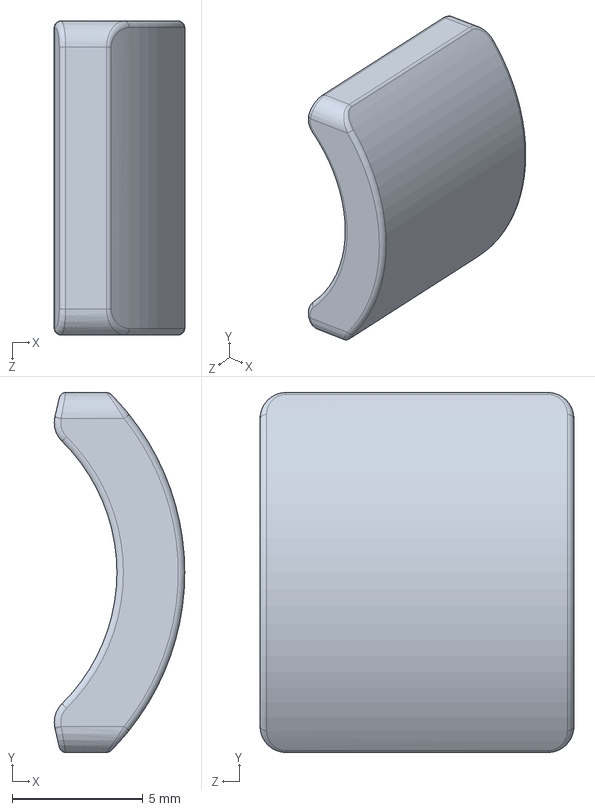
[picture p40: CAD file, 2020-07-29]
Mechanical Design/Solidworks_design/dc-motor-2/motor/Part4.SLDPRT
4.99 x 13.8 x 12.0 mm

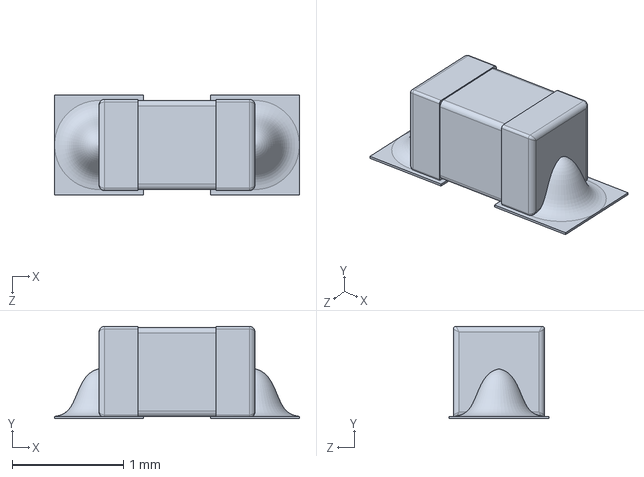
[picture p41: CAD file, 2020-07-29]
Mechanical Design/Solidworks_design/mpu-92-65-1.snapshot.2/MPU 92_65/C1.SLDPRT
2.20 x 0.83 x 0.9 mm

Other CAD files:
Mechanical Design/Solidworks_design/top.SLDPRT
Mechanical Design/Solidworks_design/dc-motor-2/motor/Part1.SLDPRT
Mechanical Design/Solidworks_design/mpu-92-65-1.snapshot.2/MPU 92_65/C2.SLDPRT
Mechanical Design/Solidworks_design/dc-motor-2/motor/Part2.SLDPRT
Mechanical Design/Solidworks_design/dc-motor-2/motor/Part3.SLDPRT
Mechanical Design/Solidworks_design/dc-motor-2/motor/Part7.SLDPRT
Mechanical Design/Solidworks_design/l298n-stepper-motor-driver-red-1.snapshot.3/L298N Stepper Motor Driver (Red).SLDPRT
Mechanical Design/Solidworks_design/mpu-92-65-1.snapshot.2/MPU 92_65/R1.SLDPRT
Mechanical Design/Solidworks_design/mpu-92-65-1.snapshot.2/MPU 92_65/V1.SLDPRT

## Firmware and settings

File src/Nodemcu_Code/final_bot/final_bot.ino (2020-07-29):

#include <MPU9250.h>
#include <ESP8266WebServer.h>
#include <string.h>
#include <math.h>
#include <ESP8266WiFi.h>
#include <ESP8266HTTPClient.h>
MPU9250 IMU;
ESP8266WebServer server(80);
//int i=0,j=0,k=0,l=0,m=0,n=0;
 float angle=0.00;
double t;
int16_t gyro[3] = {0, 0, 0};
int16_t acc[3] = {0, 0, 0};
float gyroBias[3]  = {0, 0, 0};
float accelBias[3] = {0, 0, 0};
int dt;
long Time;
float a;
int X;
int Y;
float O;
int S=-1;
double x = 0.0, y = 0.0;
double cosine , sine;
double offset;
int xf[1]={400};
int yf[1]={400};
float of[1]={90};
float oi;
const float rad =57.2958; 
const int inputPin1  = D7;//n4    
const int inputPin2  = D6;//n3
const int inputPin3  = D5;//n2   
const int inputPin4  = D4;//n1
const int inputPin5  = D3; //left  
const int inputPin6  = D8;//right
const char *ssid = "LAPTOP-2QO9LQOJ 0442"; /////////////////////////// NAME OF WIFI
const char *password = "12345678"; /////////////////// WIFI PASSWORD
String payload;
String dir;
void handleSpecificArg() 
{
 payload = "";

if (server.arg("direction")== "")
{     //Parameter not found

payload = ""; }

else
{     //Parameter found

payload = "direction = ";
dir = server.arg("direction");
payload += dir;     //Gets the value of the query parameter
// Serial2.print(dir); //Write the serial data
    delay(1000);

}
Serial.println(payload);

server.send(200, "text/plain", payload);          //Returns the HTTP response

}
void backward()
{
  digitalWrite(inputPin1, LOW);
    digitalWrite(inputPin2,HIGH);
    digitalWrite(inputPin3,LOW);
    digitalWrite(inputPin4,HIGH);
    analogWrite(inputPin5,330);
    analogWrite(inputPin6,320); 
    Serial.println("backward");
}
void forward()
{
 digitalWrite(inputPin1, HIGH);
    digitalWrite(inputPin2,LOW);
    digitalWrite(inputPin3,HIGH);
    digitalWrite(inputPin4,LOW);
    analogWrite(inputPin5,350);
    analogWrite(inputPin6,350);
     Serial.println("forward");
}
void right(float q)
{
  int i=0;
  while(i==0){
    data();
    digitalWrite(inputPin1, LOW);
    digitalWrite(inputPin2,HIGH);
    digitalWrite(inputPin3,HIGH);
    digitalWrite(inputPin4,LOW);
    analogWrite(inputPin5,320);
    analogWrite(inputPin6,320);  
    Serial.println("right");
    float r = get_gyro();
    Serial.println(r);
    if(get_gyro()<q)
    {
      pause();
     // data();
      i=1;
    }
  }
}
int k = 0;
void left(float p)
{
 
  while (k == 0) {
    data();
    digitalWrite(inputPin1, HIGH);
    digitalWrite(inputPin2, LOW);
    digitalWrite(inputPin3, LOW);
    digitalWrite(inputPin4, HIGH);
    analogWrite(inputPin5, 350);
    analogWrite(inputPin6, 350);
    Serial.println("left");
    float r = get_gyro();
    Serial.println(r);
    if (get_gyro() > p)
    {
      pause();
      Serial.println("pause");
      //data();
      k = 1;
    }
  }
}
void pause()
{
    digitalWrite(inputPin1, LOW);
    digitalWrite(inputPin2,LOW);
    digitalWrite(inputPin3,LOW);
    digitalWrite(inputPin4,LOW);
    analogWrite(inputPin5,0);
    analogWrite(inputPin6,0); 
     Serial.println("pause"); 
}
float get_gyro()
{
  IMU.readGyroData(gyro);
  dt = micros() - Time;
  angle = angle + (gyro[2] - a) * dt / 131.0 / 1000000.0;
  Time = micros();
  //  IMU.readAccelData(acc);

  //Serial.println(offset);
  return angle;

}
void setup () {
  Serial.begin(9600);
 for (int i = 0; i < 1000; i++) {
    IMU.readGyroData(gyro);
    //    gyroBias[2] += gyro[2];
    a += gyro[2];
  }
  a = a / 1000;
  //  gyroBias[2] = gyroBias[2]/1000;
  Time = micros();
    pinMode(inputPin1, OUTPUT);
    pinMode(inputPin2, OUTPUT);
    pinMode(inputPin3, OUTPUT);
    pinMode(inputPin4, OUTPUT); 
    pinMode(inputPin5,OUTPUT );
    pinMode(inputPin6, OUTPUT);
    analogWrite(inputPin5,0 );
    analogWrite(inputPin6,0);

  WiFi.begin(ssid, password);
 
  while (WiFi.status() != WL_CONNECTED) {
 
    delay(1000);
    Serial.println("Connecting..");
 
  }
  Serial.println("Connected to WiFi Network");
 Serial.print("Connected");
  Serial.print("Connected, IP address: ");
  Serial.println(WiFi.localIP());

///////////////////////////////////////////////////////////

server.on("/specificArgs", handleSpecificArg);
server.begin();

Serial.println("HTTP server started");
}


void data()
{
  int e=0;
server.handleClient();
int a=payload.indexOf("O");
int b=payload.indexOf("A");
int c=payload.indexOf("B");
int d=payload.indexOf("C");
 e=payload.indexOf("D");
 //Serial.println(e);
if(e>0)
{
  //Serial.println(1);
String subo=payload.substring(a+1,b);
String subx=payload.substring(b+1,c);
String suby=payload.substring(c+1,d);
String subs=payload.substring(d+1,e);
 X=subx.toInt();
 Y=suby.toInt();
 O=subo.toFloat();//current angle from x axis
 S=subs.toInt();
/*Serial.println(X);
Serial.println(Y);
Serial.println(O);
Serial.println(S);*/
int xd=xf[S]-X;
int yd=yf[S]-Y;
if(xd>0&&yd>0)
oi=atan(yd/xd)*rad;
if(xd<0&&yd>0)
oi=180+(atan(xd/yd)*rad);
if(xd<0&&yd<0)
oi=180+(atan(xd/yd)*rad);
if(xd>0&&yd<0)
oi=360-(atan(xd/yd)*rad);  
if(xd==0)
{
  if(yd>0)
    oi=90;
  else
  oi=270;
}
if(yd==0){
  if(xd>0)
  oi=0;
  else
  oi=180;
}
}
}
int g=0,h=1,p=-10;
void loop() {
 data();
 Serial.println(oi);
 if(p!=S)
 {
 if(S>-1)
 {
float angledi=-oi;
if(angledi>0)
 left(angledi);
else{
 right(angledi);
}
  while(h>0)
  { 
    data();
if(X>xf[S]+80||X<xf[S]-80||Y>yf[S]+80||Y<yf[S]-80)
//if(Y>yf[S]+80)
{
  forward();
}
else
{
pause();
h=-1;
}
/*for(int w=0;w<3;w++)
{
  backward();
}*/
}
float angledf=-of[S];
if(angledf>0)
 left(angledf);
if(angledf<0)
 right(angledf);
p=S; 
}
 }
 else{
  data();
  h=1;
  g=0;
 }
}
